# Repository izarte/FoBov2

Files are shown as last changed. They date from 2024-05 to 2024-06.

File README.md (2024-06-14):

# Fobov2
This project is the final master's work in artificial intelligence. This is the second version of [FOBO].
Fobo is a robot whose main task is to follow you to carry your heavy weights.

This version has one fixed ToF camera (RGBD), with it, the following person is detected using MobileNetV2 and tracker with SORT (code found in forked repo [mobile-net-for-fobo]) and movement and avoiding object logic is trained using reinforcement learning.

robot

Train simulation video can be found in this link <a href="https://youtu.be/na0y2CK5VwM" target="_blank">demo</a>. The real application can be seen in this video <a href="https://youtu.be/sEIGYYCS6TI" target="_blank">real-demo</a>

## Reinforcement learning
The environment is defined in [Gymnasium] integrated with the physics simulator [PyBullet]. The reinforcement learning algorithms used are SAC (Soft Actor-Critic) and PPO (Proximal Policy Optimization) giving better results with SAC.

Model inputs are:
1. Depth image normalized in [0, 1]
2. Human centroid in image pixels normalized [-1, 1] (-1 when the human is not found in image)
3. Motors speed normalized in the range [-1, 1]

Model outputs are:
1.  Left wheel speed [-1, 1]
2.  Right wheel speed [-1, 1]

To train a model it is recommended to use docker but it can be trained by defining environment variables found in [train_fobo.py]. To use train using docker modify parameters and volumes in [docker-compose-train.yaml] and execute:

```bash
docker compose up -d
```

Hyperparameters for both training algorithms can be optimized using [Optuna] framework. Like training it can be done with docker in [docker-compose-hyperparameters.yaml] to select an algorithm, volumes and GPU usage or locally with environment variable set up.

Likewise, previous usages, the evaluation of models can be done with docker [docker-compose-eval.yaml].

## Hardware
To create this robot it is necessary:
 1. Raspberry Pi 4 model B 4GB
 2. ESP32
 3. Google Coral USB Accelerator
 4. Arducam ToF
 5. Aukey Webcam FullHD USB
 6. 2x Chihai-motor CHP-36GP-555-ABHL
 7. 2x Metallic steel ball caster wheel
 8. 20x Ni-MH cells
 9. Dual H-bridge DC motor controller
 10. 2x Fan 5v

The following diagram shows how devices are connected

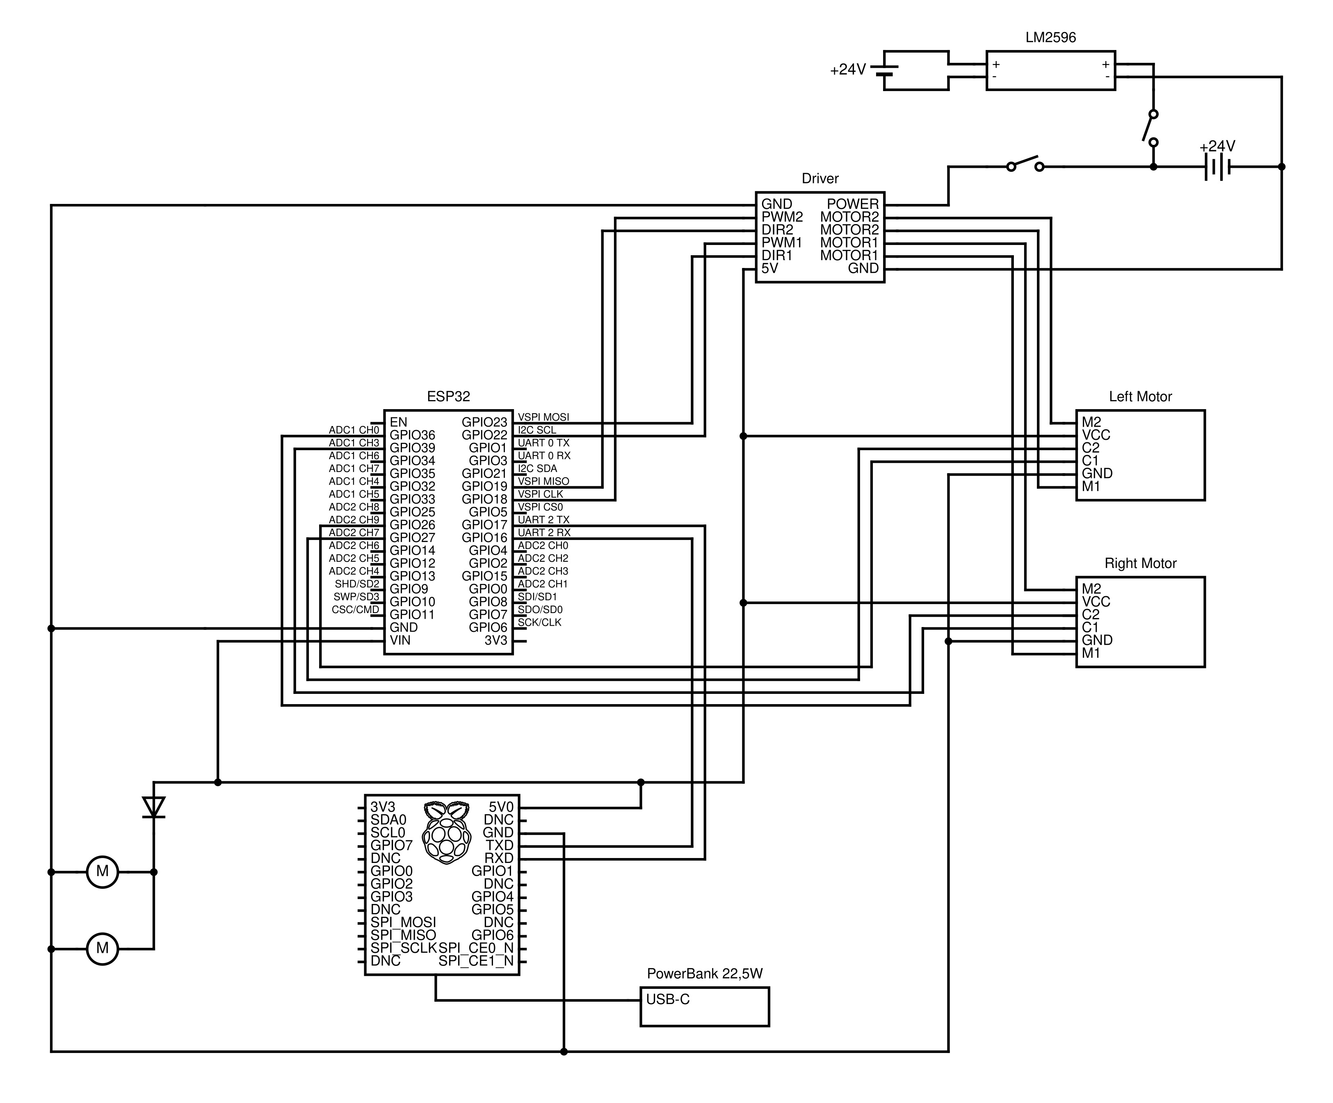
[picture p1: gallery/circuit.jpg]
circuit


## Instalation and real setup

First installation must be done following [raspberry-installation] steps and docker.

Download the forked repository for mobilenet with git submodules

```bash
git submodule init 
git submodule update
```

Go to [src] folder and execute the following command to launch all containers needed for local execution 
```bash
docker compose up -d
```

In the same folder, remotely with a 16Gb RAM execute: (This remote inferecerer should be executed previously)
```bash
docker compose -f remote-docker-compose.yaml up
```

[FOBO]: https://github.com/izarte/FoBo
[mobile-net-for-fobo]: https://github.com/izarte/object-tracker-mobile-net-fobov2
[Gymnasium]: https://github.com/Farama-Foundation/Gymnasium
[PyBullet]: https://github.com/bulletphysics/bullet3
[train_fobo.py]: https://github.com/izarte/FoBov2/blob/main/train_fobo/train_utils/train_fobo.py
[docker-compose-train.yaml]: https://github.com/izarte/FoBov2/blob/main/train_fobo/docker/docker-compose-train.yaml
[Optuna]: https://github.com/optuna/optuna
[docker-compose-hyperparameters.yaml]: https://github.com/izarte/FoBov2/blob/main/train_fobo/docker/docker-compose-hyperparameters.yaml
[docker-compose-eval.yaml]: https://github.com/izarte/FoBov2/blob/main/train_fobo/docker/docker-compose-eval.yaml
[raspberry-installation]: https://github.com/izarte/FoBov2/blob/main/raspberry/README.md
[src]: https://github.com/izarte/FoBov2/tree/main/raspberry/src
[circuit]: https://github.com/izarte/FoBov2/blob/main/gallery/circuit.jpg
[robot]: https://github.com/izarte/FoBov2/blob/main/gallery/robot.jpg

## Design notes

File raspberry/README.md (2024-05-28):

# Development

To develop this project I have use rsync to develop software in local system and send it to raspberry.

To do so, except (and rsync) package is needed, also RASP_PASSWORD should be the password ob raspbbery loaded as enviorment variable

# Instalation requirements

first plug both cameras and start

run lsusb to identify camera idVendor:idProduct

I my case I identify my device as following one
Bus 001 Device 003: ID 0c45:636d Microdia PC-LM1E
in this case idVendor=i0c45 and idProdcut=636d

sudo vim /etc/udev/rules.d/99-pi-camera.rules
ACTION=="add", ATTR{idVendor}=="0c45", ATTR{idProduct}=="636d", RUN="/bin/sh -c 'echo 0 >/sys/\$devpath/authorized'"

====OPTION 1======
check /sys/bus/usb/devices/ for list devices
got through each one reading idVendor file to identify which one is

cat /sys/bus/usb/devices/1-1.2/idVendor
0c45

add to crontab (crontab -e)
@reboot echo 1 | sudo tee /sys/bus/usb/devices/1-1.2/authorized

=====OPTION 2======
add this code to file $HOME/.utils/authorize_device.sh (make sure to create .utils folder) and give execution permissions (chmod +x $HOME/.utils/authorize_device.sh)

#!/bin/bash

# Target vendor ID
target_id="0c45"

# Base path for USB devices
base_path="/sys/bus/usb/devices"

# Iterate over all folders in the base path
for device_path in "$base_path"/*; do
    # Check if the idVendor file exists
    if [ -f "$device_path/idVendor" ]; then
        # Read the vendor ID from the file
        vendor_id=$(cat "$device_path/idVendor")

        # Check if the vendor ID matches the target ID
        if [ "$vendor_id" == "$target_id" ]; then
            # Print the matching device path
            #echo "Match found: $device_path"

            # Write 1 to the 'authorized' file of the device
            echo 1 | sudo tee "$device_path/authorized"
        fi
    fi
done

and add to crontab (crontab -e)
@reboot bash $HOME/.utils/authorize_device.sh

Give user access to google coral
sudo usermod -aG plugdev $USER

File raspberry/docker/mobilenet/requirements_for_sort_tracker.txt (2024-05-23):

filterpy==1.1.0
lap==0.4.0
svgwrite==1.4.3

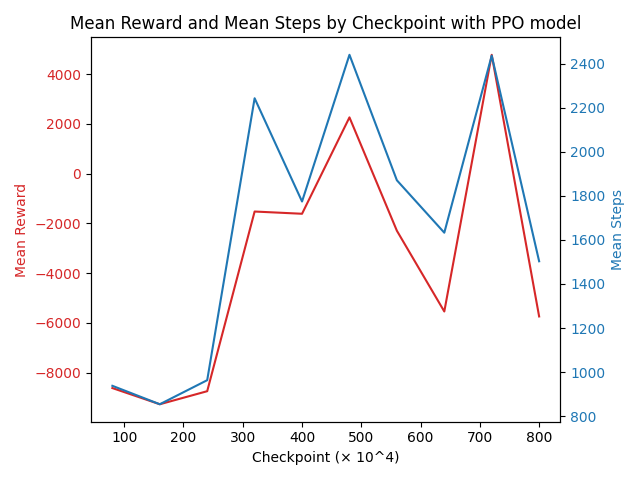
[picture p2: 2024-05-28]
train_fobo/train_utils/ppo_metrics.png

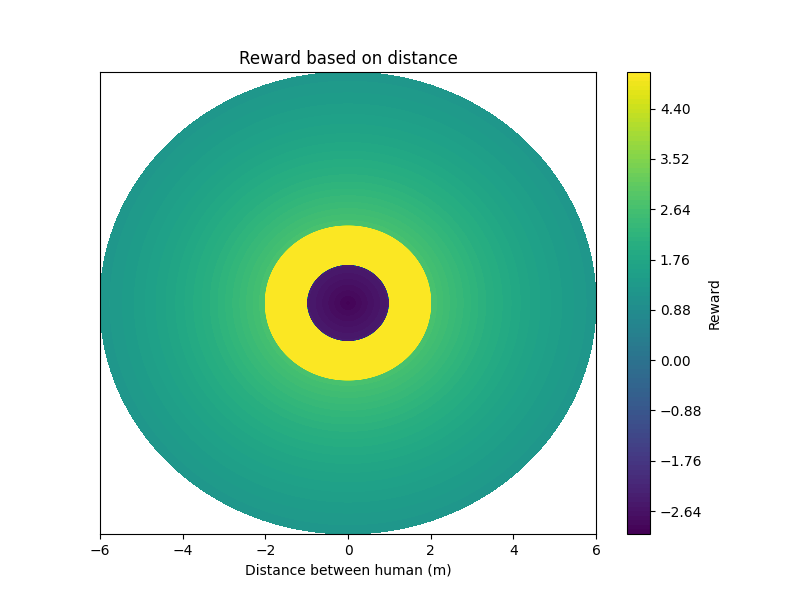
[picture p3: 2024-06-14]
train_fobo/train_utils/distance_reward_hot_map.png

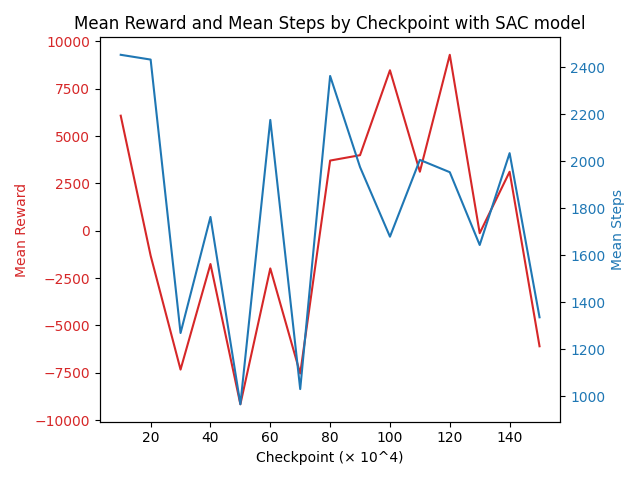
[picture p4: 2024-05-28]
train_fobo/train_utils/sac_metrics.png

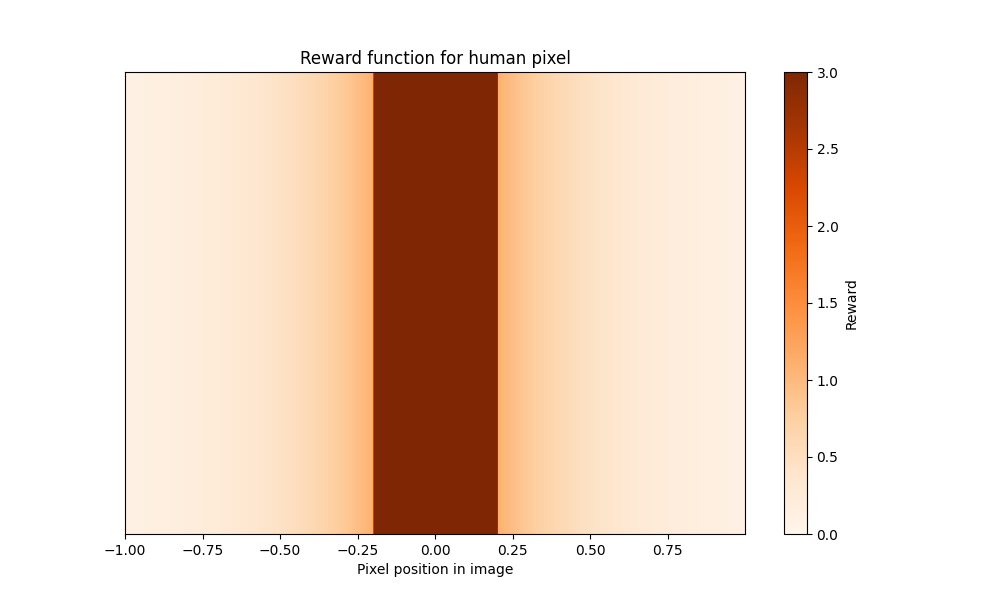
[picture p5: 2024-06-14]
train_fobo/train_utils/pixel_reward_hot_map.png

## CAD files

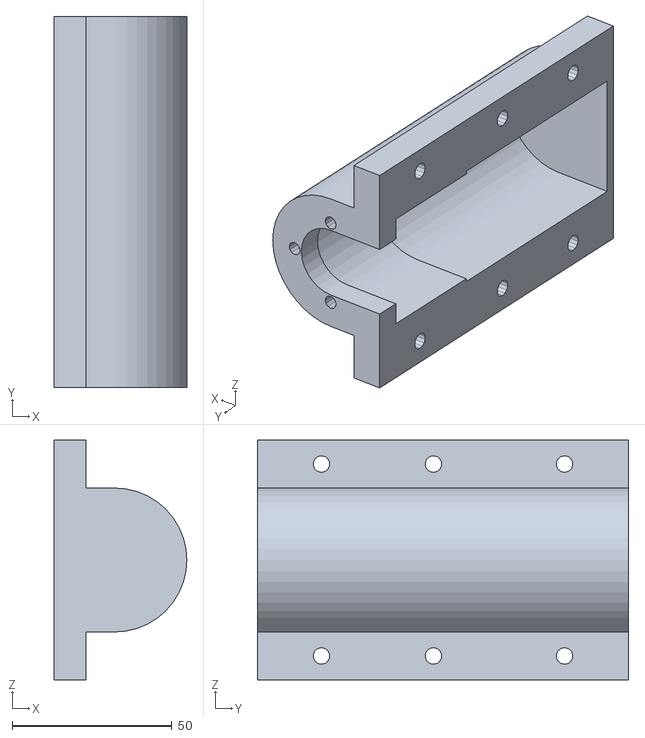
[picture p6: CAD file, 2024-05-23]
stl/motor-fastening.stl
41.5 x 116.0 x 75.0

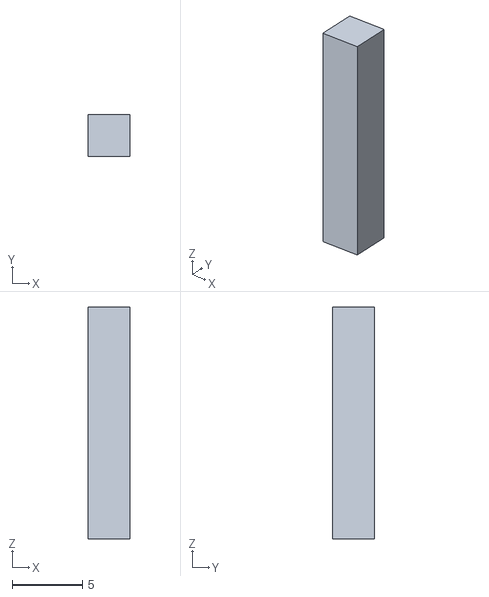
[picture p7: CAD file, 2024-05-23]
stl/camera-back-support.stl
3.00 x 3.00 x 16.5

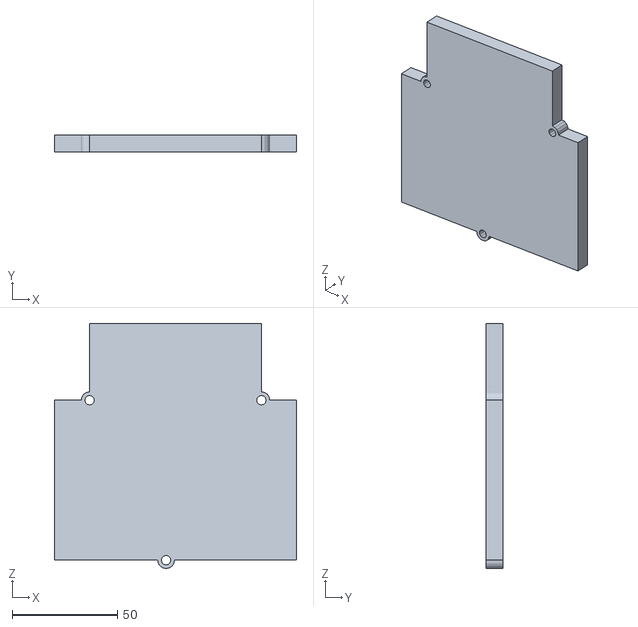
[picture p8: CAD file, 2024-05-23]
stl/raspberry-coral-chasis-fastening.stl
115.0 x 8.00 x 116.5

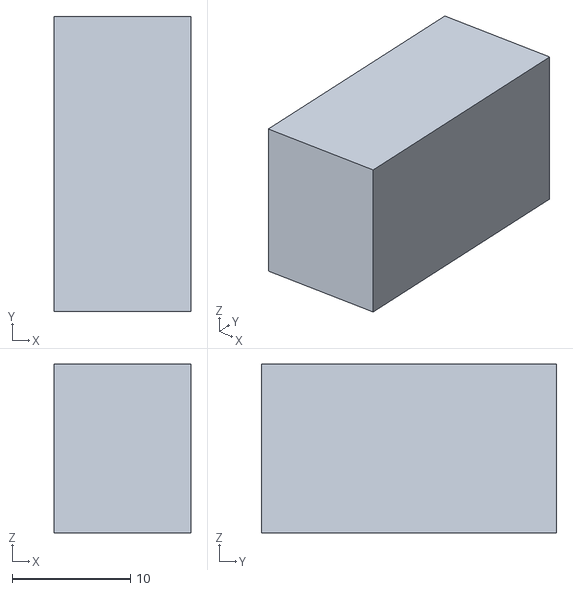
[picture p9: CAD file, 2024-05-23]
stl/camera-front-support.stl
11.6 x 25.0 x 14.3

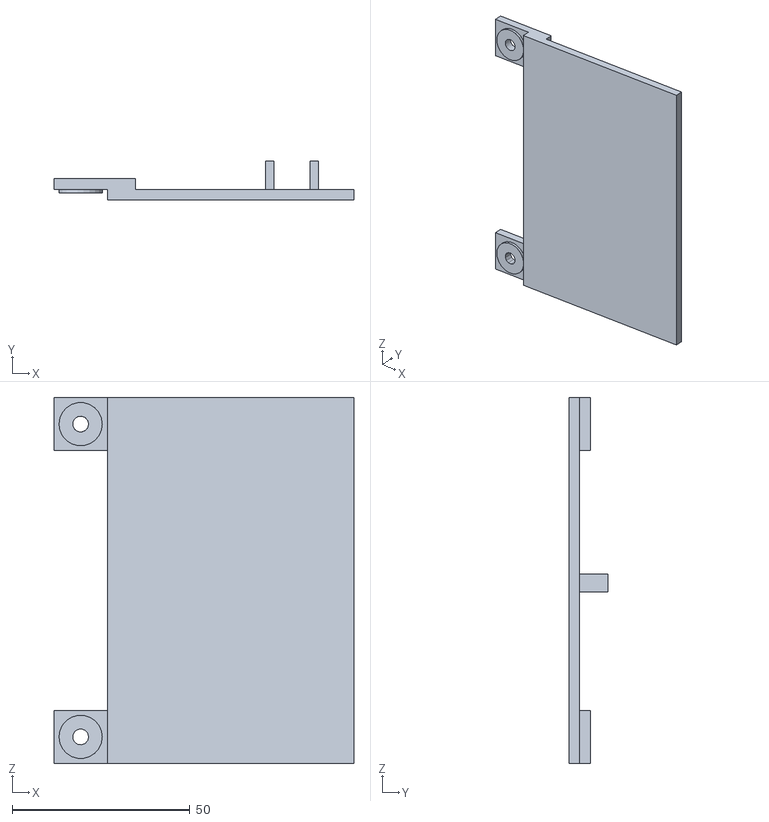
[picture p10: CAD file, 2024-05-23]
stl/chrager_adapter.stl
84.5 x 11.0 x 103.1

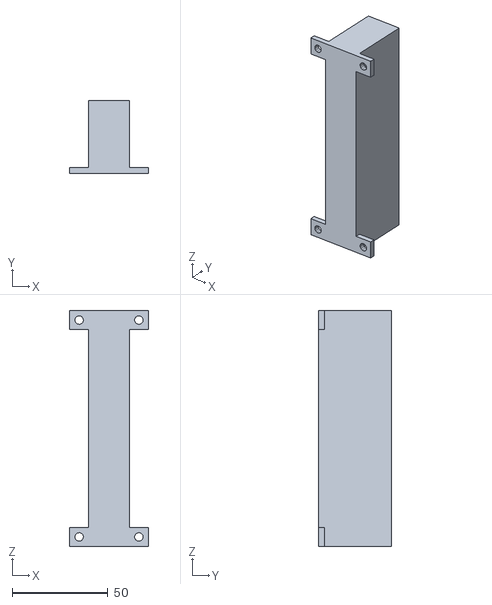
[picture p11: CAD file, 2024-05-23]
stl/HDD_fastening.stl
41.2 x 38.0 x 123.2

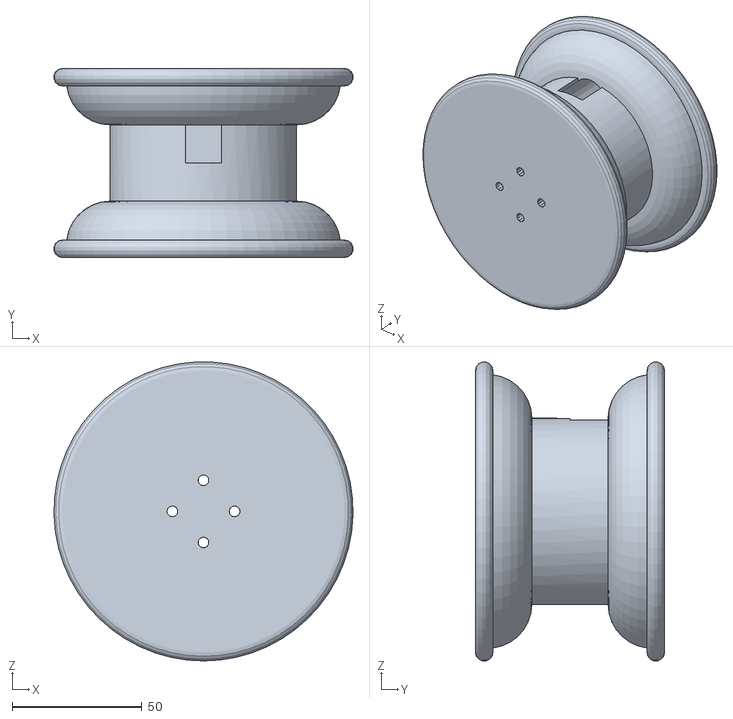
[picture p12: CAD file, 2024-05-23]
stl/wheel_coupling.stl
115.4 x 73.0 x 115.3

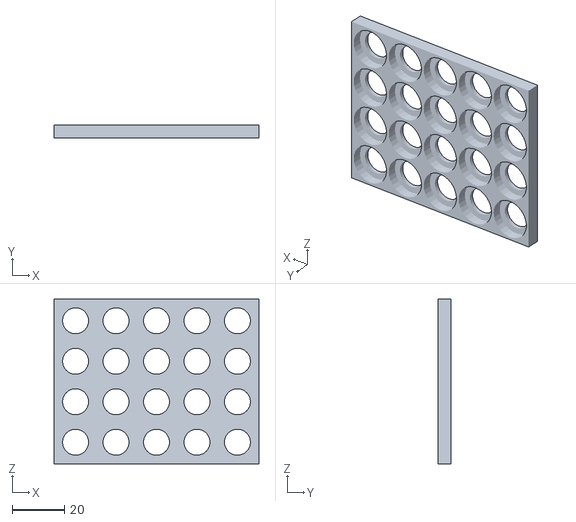
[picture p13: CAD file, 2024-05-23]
stl/battery_pack_coupling.stl
78.5 x 5.00 x 63.0

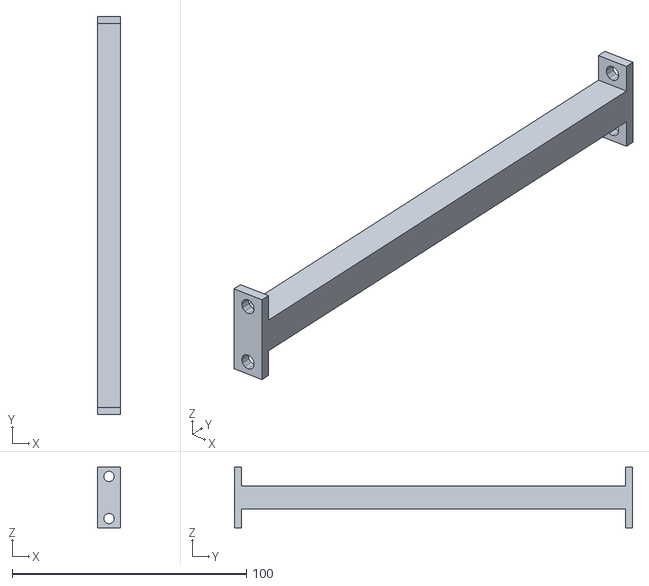
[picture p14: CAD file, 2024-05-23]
stl/basket_pilar.stl
10.0 x 170.0 x 26.0

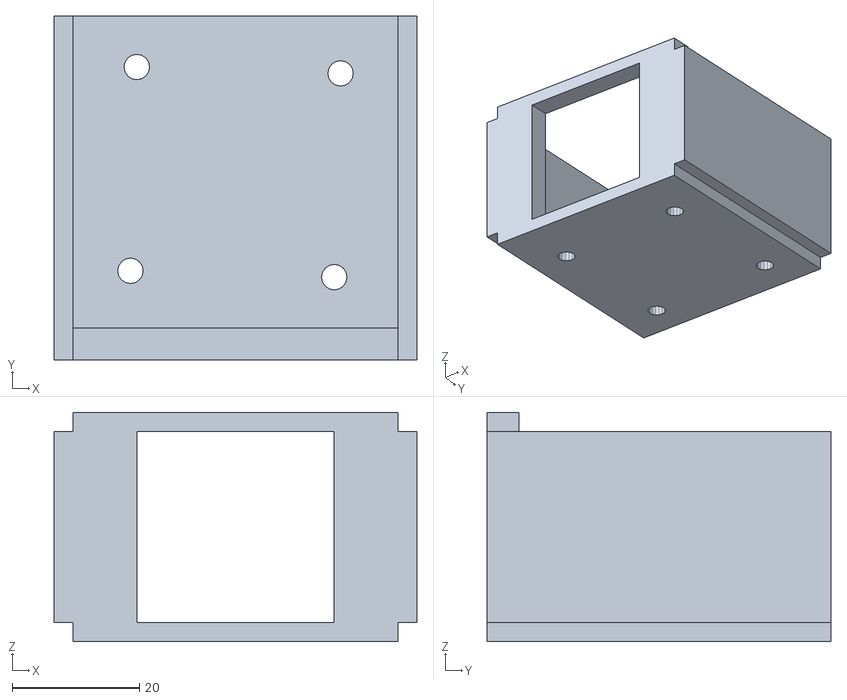
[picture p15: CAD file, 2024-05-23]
stl/depth-camera-base.stl
57.0 x 54.0 x 36.0

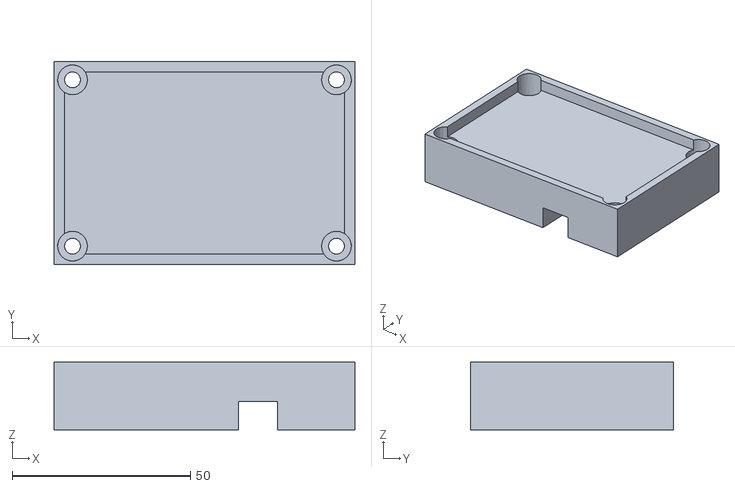
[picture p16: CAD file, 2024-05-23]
stl/bms_case.stl
84.5 x 57.0 x 19.0

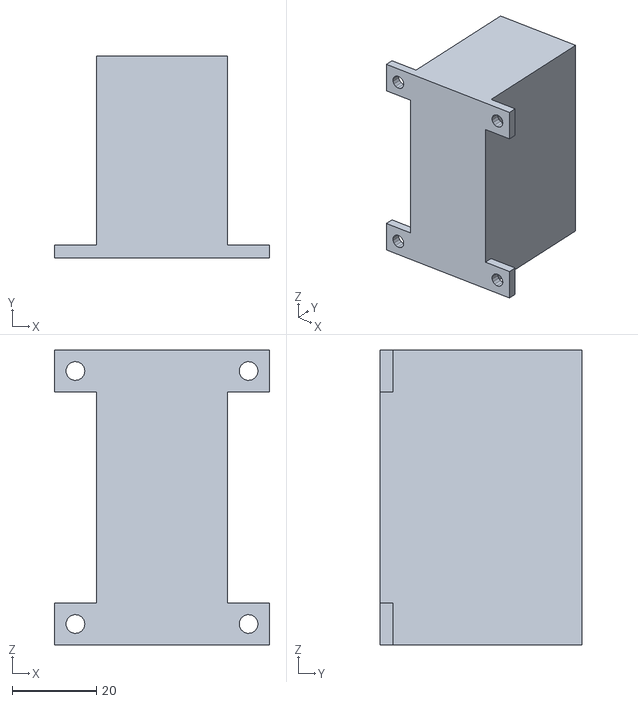
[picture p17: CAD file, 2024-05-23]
stl/rasp_battery_fastening.stl
51.2 x 48.0 x 70.2

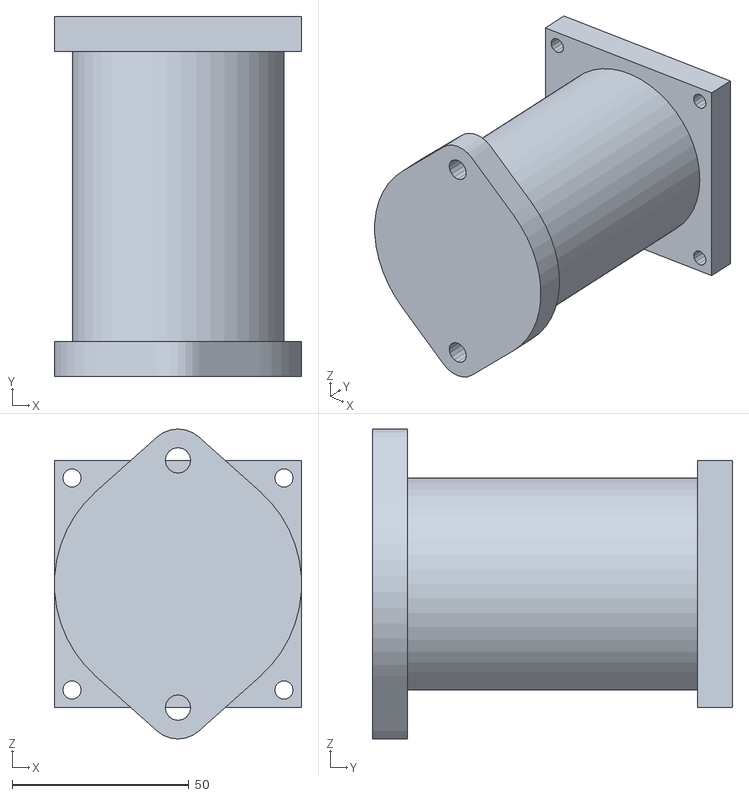
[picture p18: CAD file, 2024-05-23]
stl/ball-fastening.stl
70.0 x 102.0 x 87.8

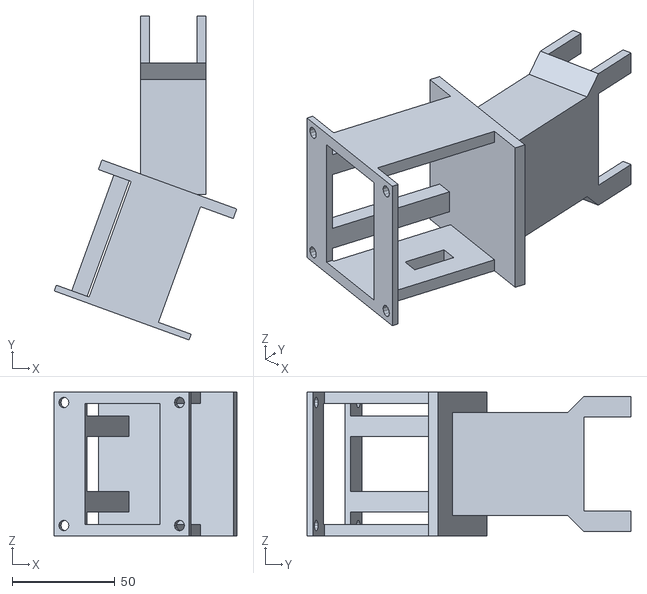
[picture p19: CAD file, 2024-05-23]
stl/camera-fastening.stl
89.0 x 158.0 x 70.0

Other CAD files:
stl/short-depth.stl
stl/battery_pack_top.stl
stl/light_indicator.stl
stl/depth-camera.stl
design/HDD_fastening.ipt
design/ball-fastening.ipt
design/basket_pilar.ipt
design/batter_pack_top.ipt
design/battery_pack_base_v0.ipt
design/battery_pack_coupling.ipt
design/battery_pack_top.ipt
design/bms_case.ipt
design/camera-back-support.ipt
design/camera-fastening.ipt
design/camera-front-support.ipt
design/chrager_adapter.ipt
design/depth-camera-base.ipt
design/depth-camera.ipt
design/depth_camera_fastening.ipt
design/light_indicator.ipt
design/motor-fastening.ipt
design/rasp_battery_fastening.ipt
design/raspberry-coral-chasis-fastening.ipt
design/short-depth.ipt
design/wheel_coupling.ipt

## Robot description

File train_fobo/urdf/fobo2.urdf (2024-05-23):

<?xml version="1.0" ?>
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
<robot xmlns:xacro="http://www.ros.org/wiki/xacro" name="fobo2">
  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
  <link name="base_link">
    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
    <inertial>
      <mass value="0.654"/>
      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
    </inertial>
  </link>
  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
  <link name="motor-right">
    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
    <inertial>
      <mass value="0.438"/>
      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
    </inertial>
  </link>
  <link name="motor-left">
    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
    <inertial>
      <mass value="0.438"/>
      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
    </inertial>
  </link>
  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
  <link name="wheel-right">
    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
    <inertial>
      <mass value="0.237"/>
      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
    </inertial>
  </link>
  <link name="wheel-left">
    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
    <inertial>
      <mass value="0.237"/>
      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
    </inertial>
  </link>
  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
  <link name="stick-front">
    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
    <inertial>
      <mass value="0.015"/>
      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
    </inertial>
  </link>
  <link name="stick-back">
    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
    <inertial>
      <mass value="0.015"/>
      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
    </inertial>
  </link>
  <link name="ball-front">
    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
    <inertial>
      <mass value="1"/>
      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
    </inertial>
  </link>
  <link name="ball-back">
    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
    <inertial>
      <mass value="1"/>
      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
    </inertial>
  </link>
  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
  <joint name="motor-right-base" type="fixed">
    <parent link="base_link"/>
    <child link="motor-right"/>
    <origin xyz="0 0.1325 -0.026000000000000002" rpy="0 1.5707 1.5707"/>
  </joint>
  <joint name="motor-left-base" type="fixed">
    <parent link="base_link"/>
    <child link="motor-left"/>
    <origin xyz="0 -0.1325 -0.026000000000000002" rpy="0 1.5707 1.5707"/>
  </joint>
  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
  <joint name="wheel-motor-right" type="continuous">
    <parent link="motor-right"/>
    <child link="wheel-right"/>
    <origin xyz="0 0 0.0965" rpy="0 0 0"/>
    <axis xyz="0 0 -1"/>
  </joint>
  <joint name="wheel-motor-left" type="continuous">
    <parent link="motor-left"/>
    <child link="wheel-left"/>
    <origin xyz="0 0 -0.0965" rpy="0 0 0"/>
    <axis xyz="0 0 -1"/>
  </joint>
  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
  <joint name="stick-back-base" type="fixed">
    <parent link="base_link"/>
    <child link="stick-back"/>
    <origin xyz="0.22500000000000003 0 -0.051" rpy="0 0 0"/>
  </joint>
  <joint name="stick-front-base" type="fixed">
    <parent link="base_link"/>
    <child link="stick-front"/>
    <origin xyz="-0.22500000000000003 0 -0.051" rpy="0 0 0"/>
  </joint>
  <joint name="ball-front-joint" type="spherical">
    <parent link="base_link"/>
    <child link="ball-front"/>
    <origin xyz="0.22500000000000003 0 -0.115" rpy="0 0 0"/>
    <axis xyz="0 0 1"/>
  </joint>
  <joint name="ball-back-joint" type="spherical">
    <parent link="base_link"/>
    <child link="ball-back"/>
    <origin xyz="-0.22500000000000003 0 -0.115" rpy="0 0 0"/>
    <axis xyz="0 0 1"/>
  </joint>
</robot>

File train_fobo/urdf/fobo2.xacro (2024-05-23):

<?xml version="1.0"?>

<robot xmlns:xacro="http://www.ros.org/wiki/xacro" name="fobo2">

    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
    <xacro:property name="chassis_length" value="0.55"/>
    <xacro:property name="chassis_width" value="0.35"/>
    <xacro:property name="chassis_depth" value="0.01"/>
    <xacro:property name="chassis_mass" value="0.654"/>
    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
    <xacro:property name="motor_radius" value="0.032"/>
    <xacro:property name="motor_length" value="0.105"/>
    <xacro:property name="motor_mass" value="0.438"/>
    <xacro:property name="motor_offset" value="0.01"/>
    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
    <xacro:property name="wheel_radius" value="0.12"/>
    <xacro:property name="wheel_length" value="0.088"/>
    <xacro:property name="wheel_mass" value="0.237"/>
    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
    <xacro:property name="ball_radius" value="0.030"/>
    <xacro:property name="ball_mass" value="1"/>
    <xacro:property name="stick_offset" value="0.05"/>
    <xacro:property name="stick_radius" value="0.015"/>
    <xacro:property name="stick_mass" value="0.015"/>
    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
    <xacro:property name="stick_length" value="0.102" />


    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

    <xacro:macro name="cylinder_inertia" params="m r h">
        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 
    </xacro:macro>


    <xacro:macro name="box_inertia" params="m x y z">
        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 
    </xacro:macro>

    <xacro:macro name="sphere_inertia" params="m r">
        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 
    </xacro:macro>


    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
    <xacro:macro name="box_link" params="link_name length width depth mass color">
        <link name="${link_name}">
            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
            <inertial>
                <mass value="${mass}"/>
                <xacro:box_inertia m="${mass}" x="${length}" y="${width}" z="${depth}" />
            </inertial>
        </link>
    </xacro:macro>


<xacro:macro name="cylinder_link" params="link_name radius length mass color lateral_friction">
    <link name="${link_name}">
        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
        <inertial>
            <mass value="${mass}"/>
            <xacro:cylinder_inertia m="${mass}" r="${radius}" h="${length}" />
        </inertial>
    </link>
</xacro:macro>

    <xacro:macro name="sphere_link" params="link_name radius mass color">
        <link name="${link_name}">
            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
            <inertial>
                <mass value="${mass}"/>
                <xacro:sphere_inertia m="${mass}" r="${radius}" />
            </inertial>
        </link>
    </xacro:macro>



    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
    <xacro:macro name="static_joint" params="name parent child xyz rpy">
        <joint name="${name}" type="fixed">
            <parent link="${parent}" />
            <child link="${child}" />
            <origin xyz="${xyz}" rpy="${rpy}"/>
        </joint>
    </xacro:macro>

    <xacro:macro name="wheel_joint" params="name parent child xyz">
        <joint name="${name}" type="continuous">
            <parent link="${parent}" />
            <child link="${child}" />
            <origin xyz="${xyz}" rpy="0 0 0"/>
            <axis xyz="0 0 -1"/> 
        </joint>
    </xacro:macro>
    <xacro:macro name="sphere_joint" params="name parent child xyz">
        <joint name="${name}" type="spherical">
            <parent link="${parent}" />
            <child link="${child}" />
            <origin xyz="${xyz}" rpy="0 0 0"/>
            <axis xyz="0 0 1"/> 
        </joint>
    </xacro:macro>


    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
    <xacro:box_link link_name="base_link" length="${chassis_length}" width="${chassis_width}" depth="${chassis_depth}" mass="${chassis_mass}" color="white" />
    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
    <xacro:cylinder_link link_name="motor-right" radius="${motor_radius}" length="${motor_length}" mass="${motor_mass}" color="white" lateral_friction="0" />
    <xacro:cylinder_link link_name="motor-left" radius="${motor_radius}" length="${motor_length}" mass="${motor_mass}" color="white" lateral_friction="0" />
    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
    <xacro:cylinder_link link_name="wheel-right" radius="${wheel_radius}" length="${wheel_length}" mass="${wheel_mass}" color="black" lateral_friction="1.0" />
    <xacro:cylinder_link link_name="wheel-left" radius="${wheel_radius}" length="${wheel_length}" mass="${wheel_mass}" color="black" lateral_friction="1.0" />
    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
    <xacro:cylinder_link link_name="stick-front" radius="${stick_radius}" length="${stick_length}" mass="${stick_mass}" color="blue" lateral_friction="0" />
    <xacro:cylinder_link link_name="stick-back" radius="${stick_radius}" length="${stick_length}" mass="${stick_mass}" color="black" lateral_friction="0" />
    <xacro:sphere_link link_name="ball-front" radius="${ball_radius}" mass="${ball_mass}" color="red" />
    <xacro:sphere_link link_name="ball-back" radius="${ball_radius}" mass="${ball_mass}" color="red" />

    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
    <xacro:static_joint name="motor-right-base" parent="base_link" child="motor-right" xyz="0 ${chassis_width/2 - motor_length/2 + motor_offset} ${-(chassis_depth + motor_radius/2)}" rpy="0 1.5707 1.5707"/>
    <xacro:static_joint name="motor-left-base" parent="base_link" child="motor-left" xyz="0 ${-(chassis_width/2 - motor_length/2 + motor_offset)} ${-(chassis_depth + motor_radius/2)}" rpy="0 1.5707 1.5707"/>
    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
    <xacro:wheel_joint name="wheel-motor-right" parent="motor-right" child="wheel-right" xyz="0 0 ${motor_length/2 + wheel_length/2}"/>
    <xacro:wheel_joint name="wheel-motor-left" parent="motor-left" child="wheel-left" xyz="0 0 ${-(motor_length/2 + wheel_length/2)}"/>
    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
    <xacro:static_joint name="stick-back-base" parent="base_link" child="stick-back" xyz="${chassis_length/2 - stick_offset} 0 ${-stick_length/2}" rpy="0 0 0" />
    <xacro:static_joint name="stick-front-base" parent="base_link" child="stick-front" xyz="${-(chassis_length/2 - stick_offset)} 0 ${-stick_length/2s}" rpy="0 0 0" />
    <xacro:sphere_joint name="ball-front-joint" parent="base_link" child="ball-front" xyz="${chassis_length/2 - stick_offset} 0 ${-chassis_depth - wheel_radius + ball_radius/2}" />
    <xacro:sphere_joint name="ball-back-joint" parent="base_link" child="ball-back" xyz="${-(chassis_length/2 - stick_offset)} 0 ${-chassis_depth - wheel_radius + ball_radius/2}" />
    

</robot>

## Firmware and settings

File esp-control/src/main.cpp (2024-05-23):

#include <Arduino.h>
#include "motor/motor.h"
#include "pin_definitions.h"
#include <HardwareSerial.h>

Motor right_motor(RIGHT_PWM_PIN, RIGHT_PWM_CHANNEL, RIGHT_DIR_PIN, RIGHT_ENCODER_PIN_A, RIGHT_ENCODER_PIN_B, 0);
Motor left_motor(LEFT_PWM_PIN, LEFT_PWM_CHANNEL, LEFT_DIR_PIN, LEFT_ENCODER_PIN_A, LEFT_ENCODER_PIN_B, 1);
HardwareSerial UART1(2);


void setup() {
  Serial.begin(115200);
  right_motor.setup();
  right_motor.set_speed(0);

  left_motor.setup();
  left_motor.set_speed(0);

  UART1.begin(1500000, SERIAL_8N1, 16, 17);
}

String inputBuffer = "";
char readenChar;
int separation_idx, left_speed, right_speed;

void loop() {
  while (UART1.available()) {
    char readenChar = (char)UART1.read();
    inputBuffer += readenChar;
    if (readenChar == '\n') {
      separation_idx = inputBuffer.indexOf(' ');
      left_speed = inputBuffer.substring(0, separation_idx).toInt();
      right_speed = inputBuffer.substring(separation_idx + 1).toInt();

      left_motor.set_speed(left_speed);
      right_motor.set_speed(right_speed);

      String encoders_speed_str = String(left_motor.get_speed()) + " " + String(right_motor.get_speed());
      UART1.println(encoders_speed_str);
      inputBuffer = "";
    }
  }
}

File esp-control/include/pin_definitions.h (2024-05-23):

#ifndef PIN_DEFINITIONS_H
#define PIN_DEFINITIONS_H

#define RIGHT_ENCODER_PIN_A 39
#define RIGHT_ENCODER_PIN_B 36

#define RIGHT_DIR_PIN 19
#define RIGHT_PWM_PIN 18


#define LEFT_ENCODER_PIN_A 26
#define LEFT_ENCODER_PIN_B 25

#define LEFT_DIR_PIN 23
#define LEFT_PWM_PIN 22


#define RIGHT_PWM_CHANNEL 0
#define LEFT_PWM_CHANNEL 1

#endif

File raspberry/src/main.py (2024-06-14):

from data_reader import DataReader
from motors_control import MotorsControl
import sys
from local_inferencerer import LocalInferencer
import numpy as np
import signal
# import cv2

MAX_SPEED = 20


def signal_handler(self, sig, frame):
    import sys

    motors_control = MotorsControl()
    # # print("MAIN READY")
    _ = motors_control.move_and_read([0, 0])
    print("Signal received:", sig)
    sys.exit(0)


def main():
    # Creater reader objects
    print("START MAIN")
    yolo_reader = DataReader(port=8000, label="pixel")
    # print("YOLO WEBSOCKET READY")
    depth_reader = DataReader(port=8001, label="depth")
    # # # speeds_reader = DataReader(port=8002, label="speeds")
    # # print("DEPTH WEBSOCKET READY")
    motors_control = MotorsControl()
    # # print("MAIN READY")
    motors_speed = motors_control.move_and_read([0, 0])
    signal.signal(signal.SIGTERM, signal_handler)
    inferencer = LocalInferencer()
    print("waiting for client")
    inferencer.wait_to_client()
    print("Client detected")
    init_messages = 0
    human_pixel = {"x": 0, "y": 0}
    try:
        while True:
            # human_pixel = None
            # Read yolo data
            human_pixel = yolo_reader.read_data()
            print("pixel: ", human_pixel)
            # Read depth data
            human_pixel = yolo_reader.read_data()
            print("pixel: ", human_pixel)
            # Read depth data
            depth_image = depth_reader.read_data()
            obs = {
                "human_pixel": np.array(
                    [human_pixel["x"], human_pixel["y"]],
                    dtype=np.float32,
                ),
                "depth_image": depth_image,
                "wheels_speed": np.array(
                    motors_speed,
                    dtype=np.float32,
                ),
            }
            while init_messages < 4:
                init_messages += 1
                inferencer.send_message(obs)
            inferencer.send_message(obs)
            action = inferencer.read_message()
            print("action:", action)
            print(depth_image)
            # cv2.imshow(depth_image)
            # cv2.waitKey(1)
            # Read motors speed
            # controller_speeds = speeds_reader.read_data()
            # Scale action
            action = np.array(action) * MAX_SPEED
            # Move motors
            motors_speed = motors_control.move_and_read(action)
            # print("motors speed:", motors_speed)

    except KeyboardInterrupt:
        print("Ctrl-C pressed!")
        sys.exit(0)


if __name__ == "__main__":
    main()

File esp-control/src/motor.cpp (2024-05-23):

#include "motor/motor.h"


Motor::Motor(int pwm, int pwm_channel, int dir, int encoderA, int encoderB, bool inverse)
{
    pwm_pin = pwm;
    pwm_chan = pwm_channel;
    dir_pin = dir;
    this->encoderA = encoderA;
    this->encoderB = encoderB;
    this-> inverse = inverse;
}


void Motor::setup()
{
	// Set up pwm signals
	ledcSetup(pwm_chan, FREQ, PWM_RESOLUTION);
	ledcAttachPin(pwm_pin, pwm_chan);
	pinMode(dir_pin, OUTPUT);
	digitalWrite(dir_pin, LOW);

	digitalWrite(dir_pin, LOW);
  	ledcWrite(pwm_chan, 255 * 10 / 100);

    // Attach encoder pins
    encoder.attachHalfQuad(encoderA, encoderB);
    encoder.setCount(0);
    last_check = millis();
}


void Motor::set_speed(int speed)
{
    if (speed > 100)
        speed = 100;
    if (speed < -100)
        speed = -100;

    digitalWrite(dir_pin, speed > 0 ^ inverse);
  	ledcWrite(pwm_chan, 255 * abs(speed) / 100);
}


float Motor::get_speed()
{
    int64_t count = encoder.getCount();

    unsigned long elapsed_time = millis() - last_check;

    float elasped_time_s = elapsed_time / 1000.0; 

    float velocity = 0.065625 * count / elasped_time_s;

    last_check = millis();
    encoder.clearCount();

    return velocity;
}

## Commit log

2024-03-07 Add wheel coupling
    [wheel_coupling.ipt, wheel_coupling.stl]
2024-03-07 Add racecar simulation and wheel movement
    [chassis.STL, chassis_differential.STL, cone.obj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]
2024-03-07 Add motor test
2024-03-10 Add encoder test
2024-03-12 Add complete, not tested motor fastening design
    [motor-fastening.0004.ipt, motor-fastening.ipt, motor-fastening.stl]
2024-03-12 Add encoder test, correct functionality
    [main.cpp]
2024-03-13 Add motor class
2024-03-16 Add ball-fastening prototype
    [ball-fastening.ipt, ball-fastening.stl]
2024-03-17 Add length for piece
    [ball-fastening.ipt, ball-fastening.stl]
2024-03-22 Increment ball fastening length
    [ball-fastening.ipt, ball-fastening.stl]
2024-03-27 Add dockcerfile for ToF image with drivers installed
2024-03-27 Add final ball-fastening model
    [ball-fastening.ipt, ball-fastening.stl]
2024-03-29 Start creating robot urdf xacro
    [fobo2.xacro]
2024-03-30 Add base model in xacro with urdf converter
    [differential_robot.urdf, fobo2.urdf, fobo2.xacro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]
2024-03-31 Add human urdf
    [human.urdf]
2024-03-31 Chassis robot, simulation of walking and camera movement
    [fobo2.urdf, fobo2.xacro]
2024-04-01 Add basic room urdf
    [room.urdf, room.xacro]
2024-04-01 Remove unnecessary meshes
    [chassis.STL, chassis_differential.STL, cone.obj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]
2024-04-02 Update gym env, Add robot class
    [fobo2.urdf]
2024-04-02 Add camera position and orientation based on robot
2024-04-02 Add reward function, and motor speed retrival
2024-04-03 Properly adjust camera relative position, add human class, add world class with basic room, add initial random position divided
    [human.urdf, wall.urdf]
2024-04-10 Add depth piece short version
    [short-depth.ipt, short-depth.stl]
2024-04-10 add depth camera model for long version
    [depth-camera.ipt, depth-camera.stl]
2024-04-10 Add camera coupling for depth camera with adjustment parts due to model ipt loss
    [camera-back-support.ipt, camera-back-support.stl, camera-front-support.ipt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]
2024-04-10 Add camera-fastening stl
    [camera-fastening.stl]
2024-04-12 Add new small design for battery pack
    [battery_pack_base.ipt, battery_pack_base.stl]
2024-04-12 Add battery pack base and rename base to coupling
    [battery_pack_base.ipt, battery_pack_base.stl, battery_pack_coupling.ipt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]
2024-04-12 Add motor class and removed old classes
2024-04-18 Add more realistic representation of real robot
    [fobo2.urdf, fobo2.xacro, wall.urdf]
2024-04-18 Add battery front layers for bms and light battery indicator
    [ball-fastening.ipt, bms_case.ipt, bms_case.stl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]
2024-04-21 Add input normalization and correct depth buffer memory
    [fobo2.urdf]
2024-04-21 Change urdf model and add optuna optimization hyperparams
    [fobo2.urdf, fobo2.xacro]
2024-04-23 Update lost files
    [best_a2c_hyperparameters.txt, best_sac_hyperparameters.txt]
2024-05-01 Progress with sac and ppo and modify docker compose for second ppo rovit
    [wall.urdf]
2024-05-01 Add first uart code handling
2024-05-01 Organize folders and add main to test uart communication
2024-05-02 Add turning check and just get reward with human in camera
2024-05-08 Version 0.3.0, add random obstacles to world and logic for avoid collisions with human walk, repeat new target until trakectory is free
    [box.urdf, cylinder.urdf, sq_column.urdf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]
2024-05-13 Add battery pack models
    [batter_pack_top.ipt, battery_pack_base.stl, battery_pack_base_v0.ipt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]
2024-05-13 Add uart functional code
2024-05-14 Version 0.4.0, correct depth image, add noise to all sensors and actuators
2024-05-16 Add efficient uart communication reading char by char
2024-05-17 Add lost designs
    [camera-fastening.ipt, chrager_adapter.ipt, chrager_adapter.stl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]
2024-05-17 Organize stl designs
    [ball-fastening.stl, battery_pack_coupling.stl, battery_pack_top.stl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]
2024-05-19 Add hdd, raspberry battery and basket pilar fasetnings
    [HDD_fastening.ipt, HDD_fastening.stl, basket_pilar.ipt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]
2024-05-21 Add new hyperparametrs for sac
    [best_sac_hyperparameters.txt]
2024-05-23 Organize in folder train_fobo
    [best_a2c_hyperparameters.txt, best_sac_hyperparameters.txt, box.urdf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]
2024-05-23 Organize urdft too in folder train_fobo
    [fobo2.urdf, fobo2.xacro, human.urdf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]
2024-05-23 Organize instalattion method in raspberry readme
2024-05-23 Fix negative speed handeling
    [main.cpp, motor.cpp]
2024-05-26 Add optuna hyperparameters results ad trains based on those hyperparams
    [best_a2c_hyperparameters.txt, best_ppo_hyperparameters.txt]
2024-06-14 Add circuit image
